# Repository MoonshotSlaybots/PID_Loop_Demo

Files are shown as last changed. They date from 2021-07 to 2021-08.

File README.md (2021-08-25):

# PID_Loop_Demo
Arduino project to demonstrate how to tune a PID controller

## [Wiki](https://github.com/MoonshotSlaybots/PID_Loop_Demo/wiki)

## Wiring Diagram
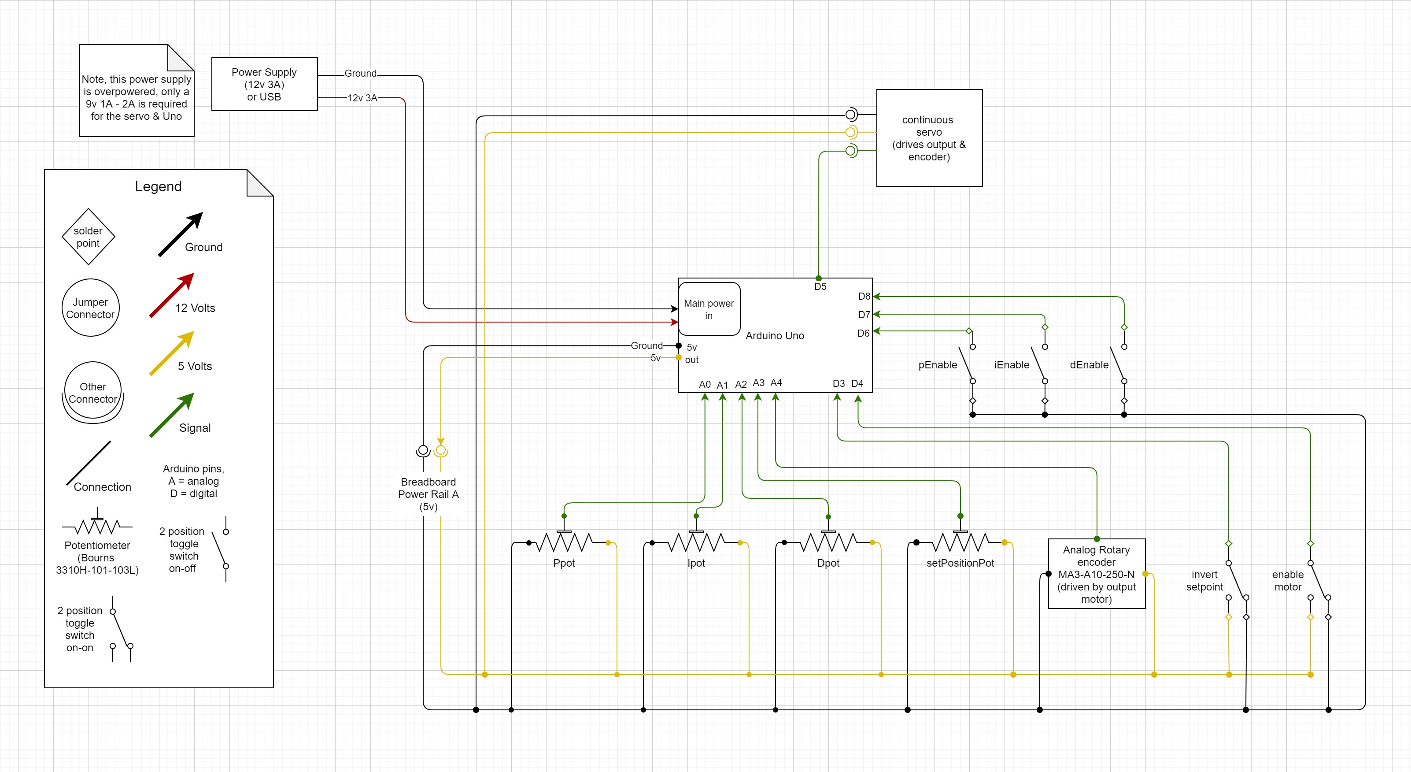
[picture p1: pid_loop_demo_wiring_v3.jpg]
Wiring Diagram


## Major Tools Needed
- 3D printer (small parts)
- Laser cutter (at least 12 in. by 6 in.)

## Hardware list
- 1 x [Arduino Uno](https://store.arduino.cc/usa/arduino-uno-rev3)
- 4 x [10Kohm Potentiometer](https://www.mouser.com/ProductDetail/Bourns/3310H-101-103L?qs=gTYE2QTfZfRCK85Ji3ROkA%3D%3D)
- 1 x [Continuous Servo (HSR-1425CR)](https://www.andymark.com/products/hi-tec-servo-model-hsr-1425cr?sku=am-2587)
- 3 x [ON - OFF Toggle Switches](https://www.amazon.com/mxuteuk-Terminal-Position-Miniature-Dashboard/dp/B07QGDDTWJ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)
- 2 x ON - ON Toggle Switches
- 24 x [Hex Drive Flat Head Screw, 10-32 Thread Size, 3/8" Long](https://www.mcmaster.com/91253A001/)
- 24 x [Brass Heat-Set Inserts for Plastic](https://www.mcmaster.com/97171A200/)
- 3mm plywood for laser cut
- PLA Filament for 3D print

## Known Issues
- Running the servo power on the same circuit as the inputs causes significant voltage drops when the servo starts moving. The input potentiometers see this voltage change as a change in the input and creates noise in the system. This is because the inputs are analog and sensitive to voltage changes. This could be corrected by isolating the control circuit from the servo power draw or by using a digital method for the input, such as pwm. 
- Crossing from -180 deg to 180 deg creates a hiccup in the system. This is likely due to the smoothing algorithm trying to smooth the large change in angle rather than an instantaneous change as it should be.
- High Kd values cuases jitter in the system, this is likely related to the power draw issue listed ealier.

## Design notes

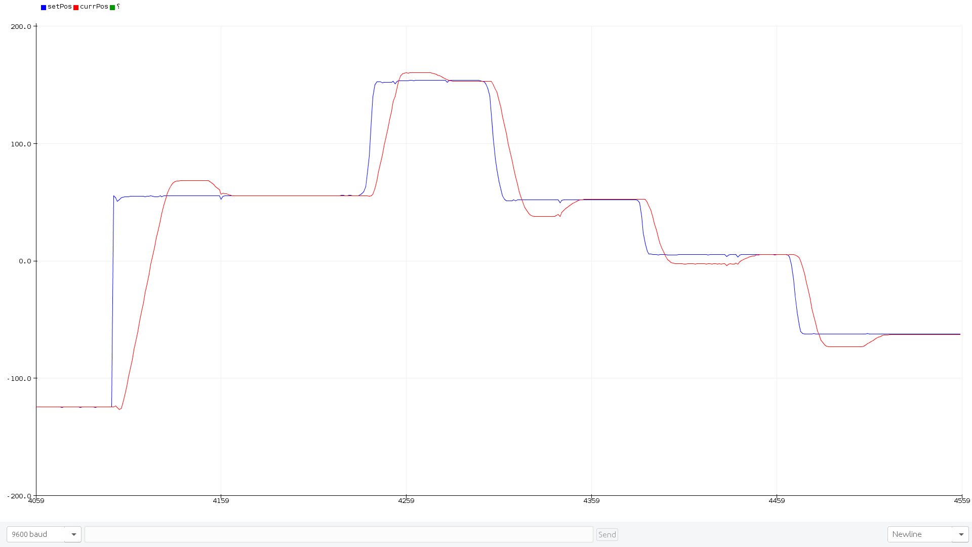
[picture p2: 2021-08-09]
images/PI_good.png

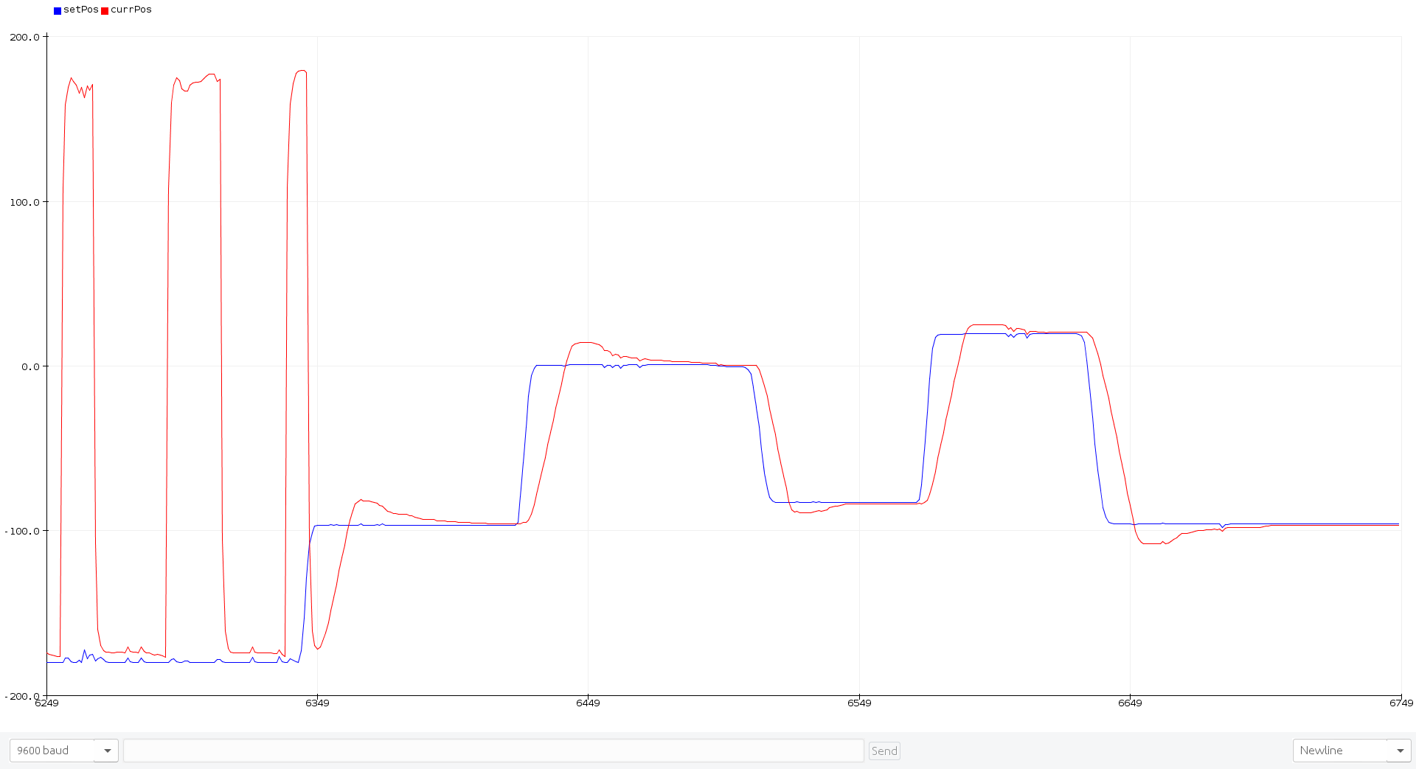
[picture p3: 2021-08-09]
images/PID_PI_only.png

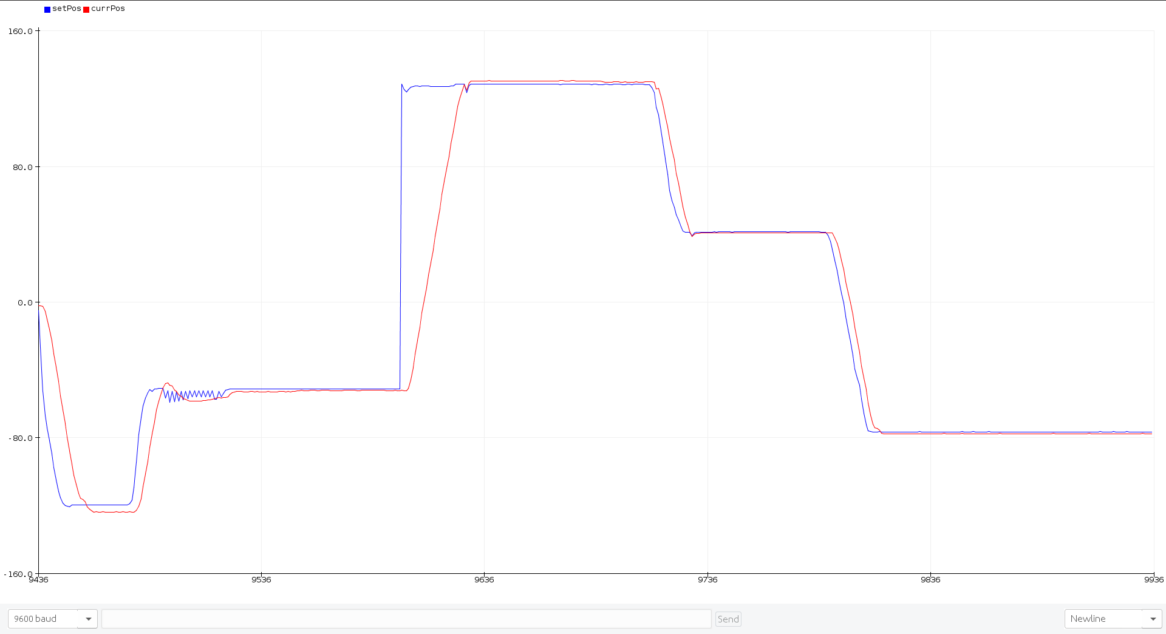
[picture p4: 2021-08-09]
images/PID_good.png

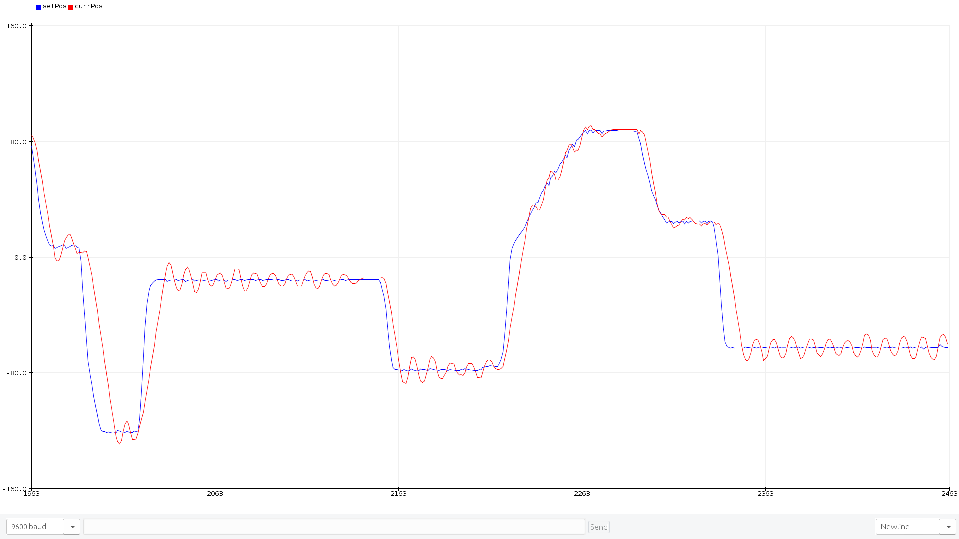
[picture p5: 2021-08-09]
images/p_too_high.png

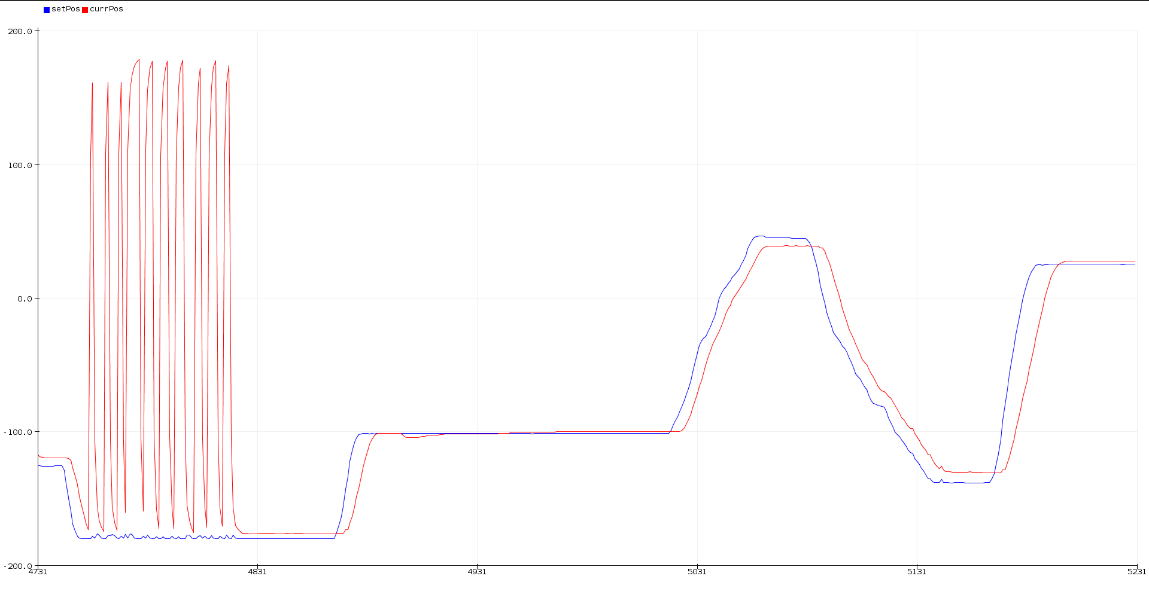
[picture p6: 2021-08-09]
images/p_good.png

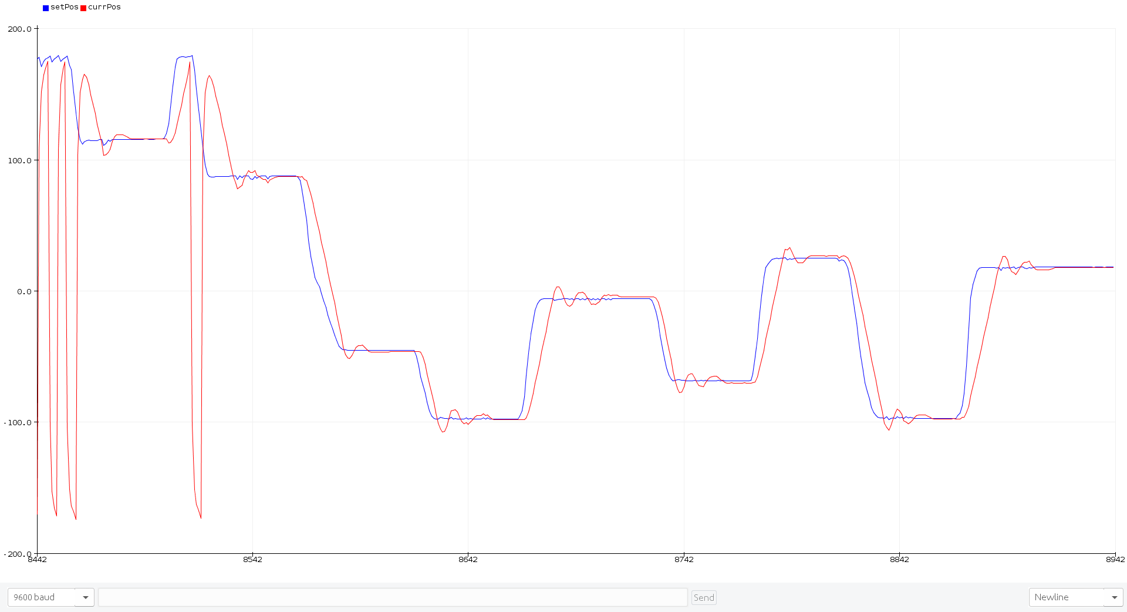
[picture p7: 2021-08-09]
images/p_little_too_high.png

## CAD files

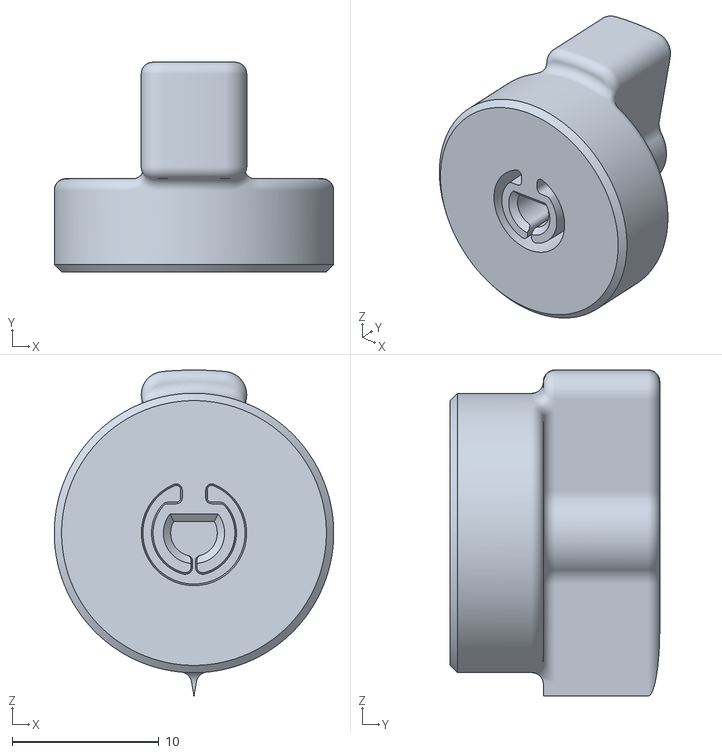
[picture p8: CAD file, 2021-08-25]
mechanical/3D_print/POT_Knob_V2.1.STL
19.0 x 14.3 x 22.2

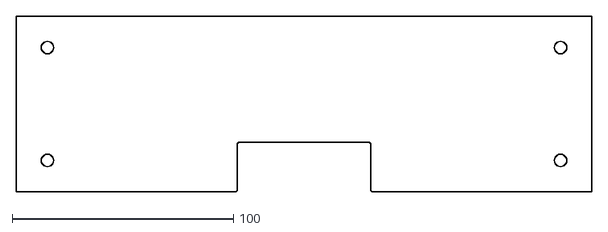
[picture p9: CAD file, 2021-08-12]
mechanical/Laser_cut/Back Panel Cut clean.dxf
260.0 x 79.2

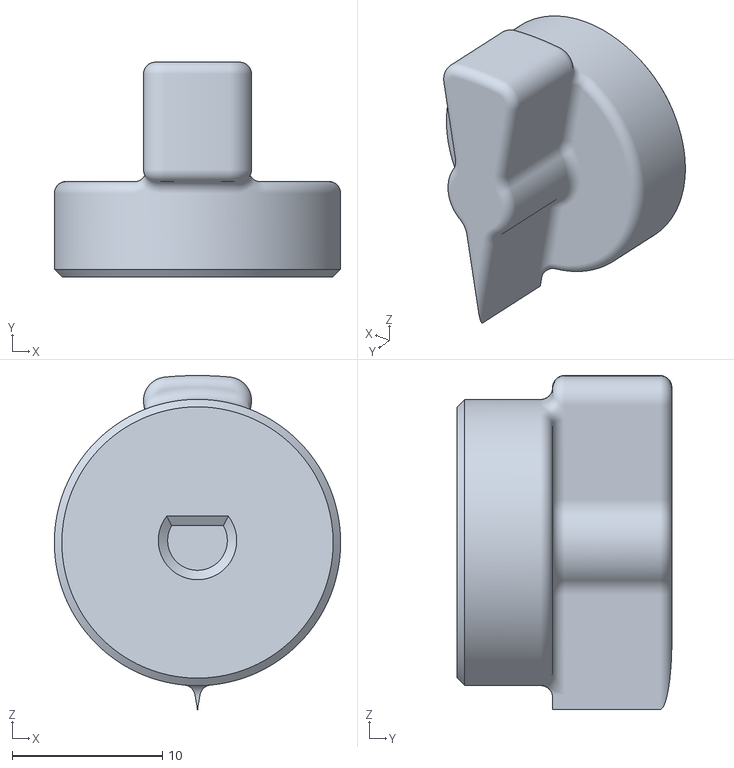
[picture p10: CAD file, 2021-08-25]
mechanical/3D_print/POT_Knob_V2_125%_hole.STL
19.0 x 14.3 x 22.2

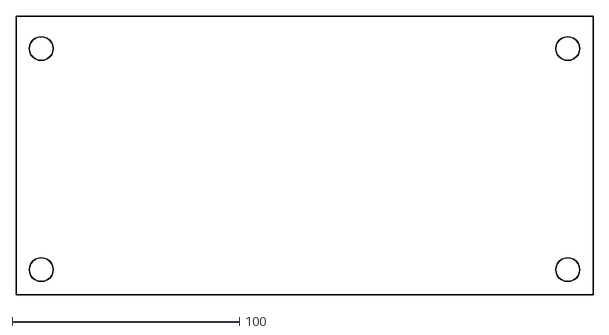
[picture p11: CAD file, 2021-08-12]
mechanical/Laser_cut/Bottom Panel Engrave clean.dxf
254.0 x 122.7

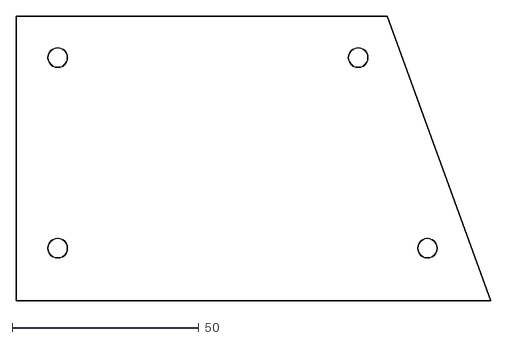
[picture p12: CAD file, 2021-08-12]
mechanical/Laser_cut/Left Panel Cut clean.dxf
127.0 x 76.2

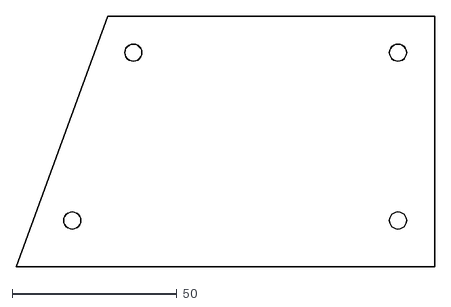
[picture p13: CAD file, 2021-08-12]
mechanical/Laser_cut/Right Panel Cut clean.dxf
127.0 x 76.2

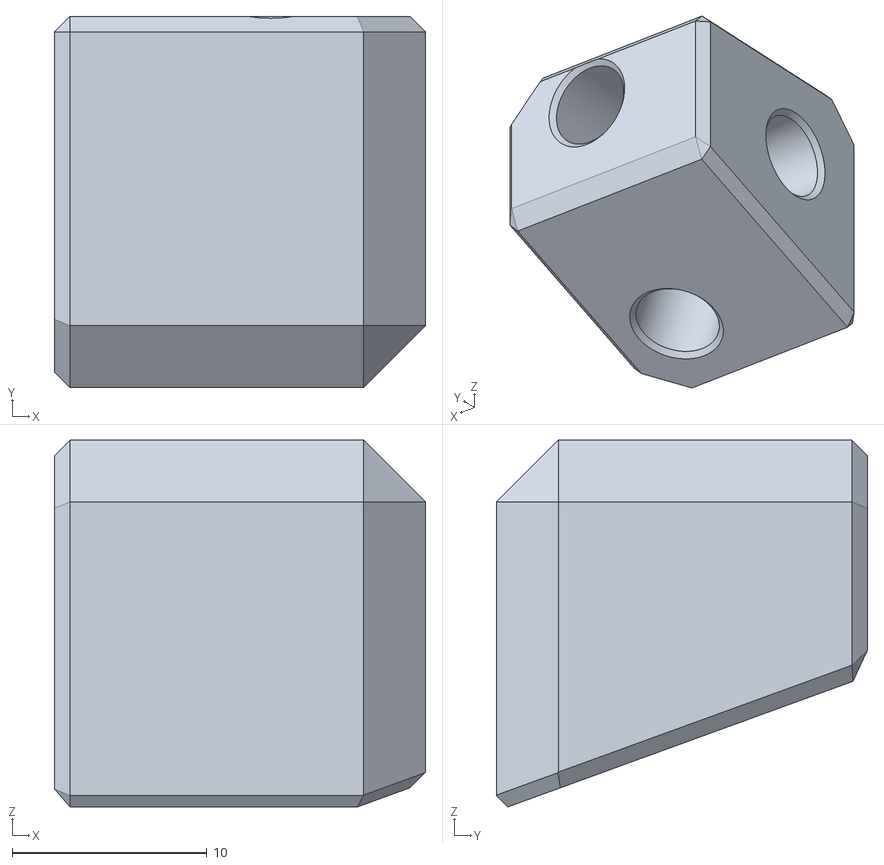
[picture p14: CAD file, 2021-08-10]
mechanical/3D_print/Front_Top_Left_Front_Corner_Block.STL
19.1 x 19.1 x 18.8

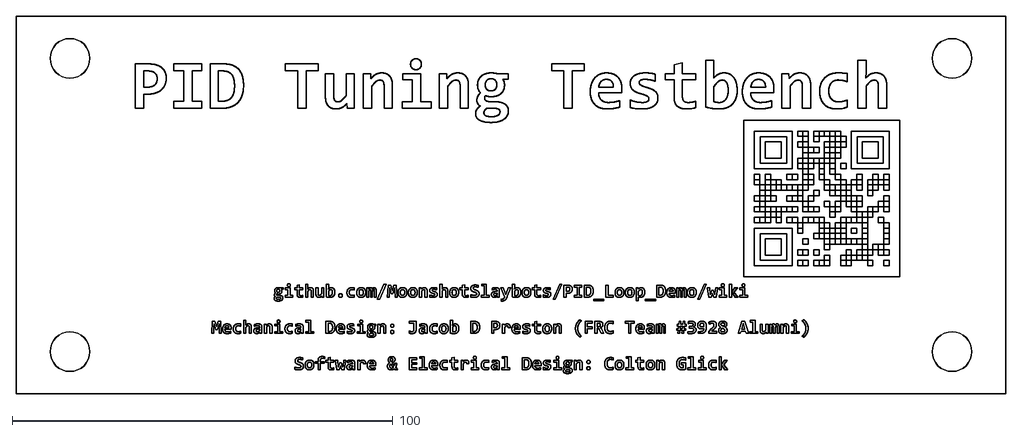
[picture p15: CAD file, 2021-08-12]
mechanical/Laser_cut/Top Panel Engrave filled.dxf
260.0 x 99.3

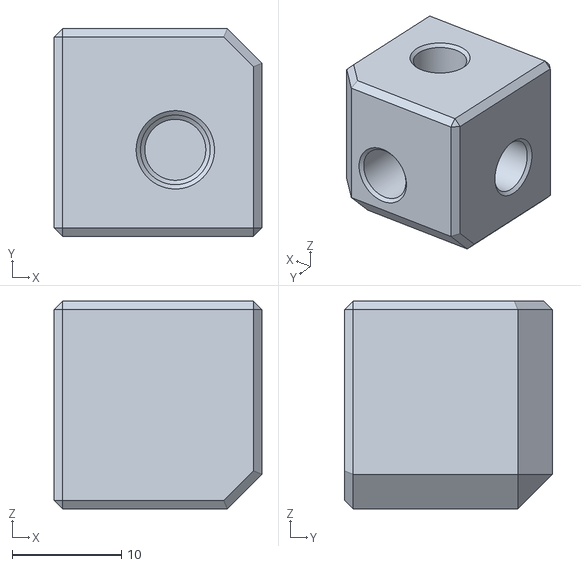
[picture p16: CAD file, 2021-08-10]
mechanical/3D_print/Back_3_Way_90_deg_Corner_Block_V1.STL
19.1 x 19.1 x 19.1

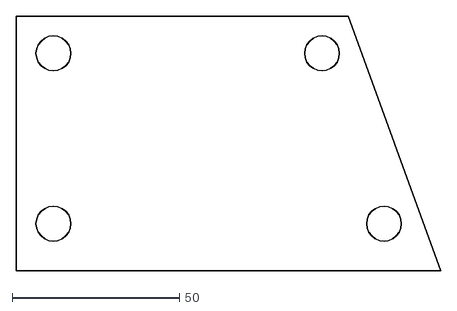
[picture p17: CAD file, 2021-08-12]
mechanical/Laser_cut/Left Panel Engrave clean.dxf
127.0 x 76.2

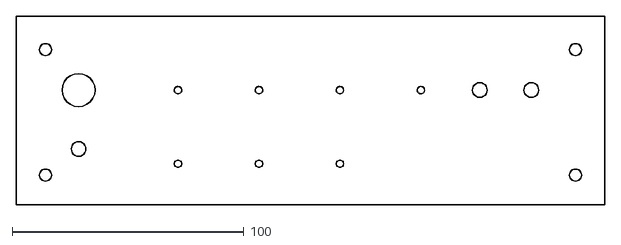
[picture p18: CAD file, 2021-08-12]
mechanical/Laser_cut/Front Panel Cut clean.dxf
254.0 x 81.1

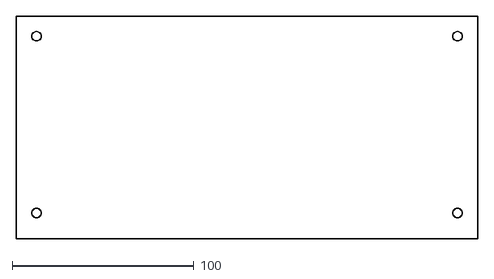
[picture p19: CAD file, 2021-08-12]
mechanical/Laser_cut/Bottom Panel Cut clean.dxf
254.0 x 122.7

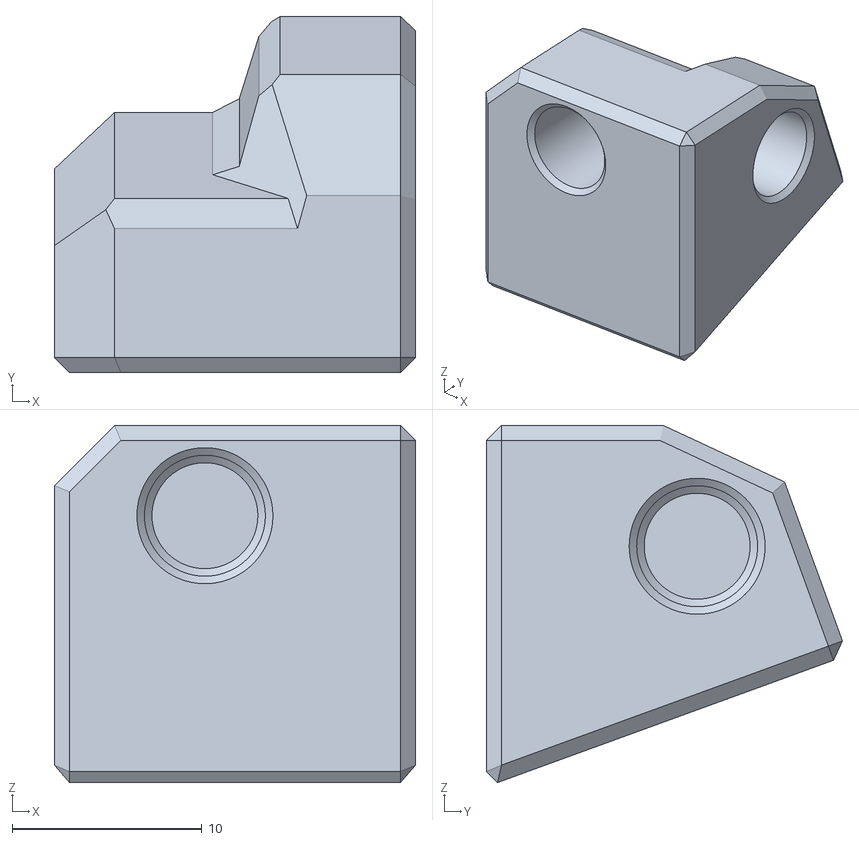
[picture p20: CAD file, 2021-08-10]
mechanical/3D_print/Front_Bottom_Right_Front_Corner_Block.STL
19.1 x 18.8 x 18.8

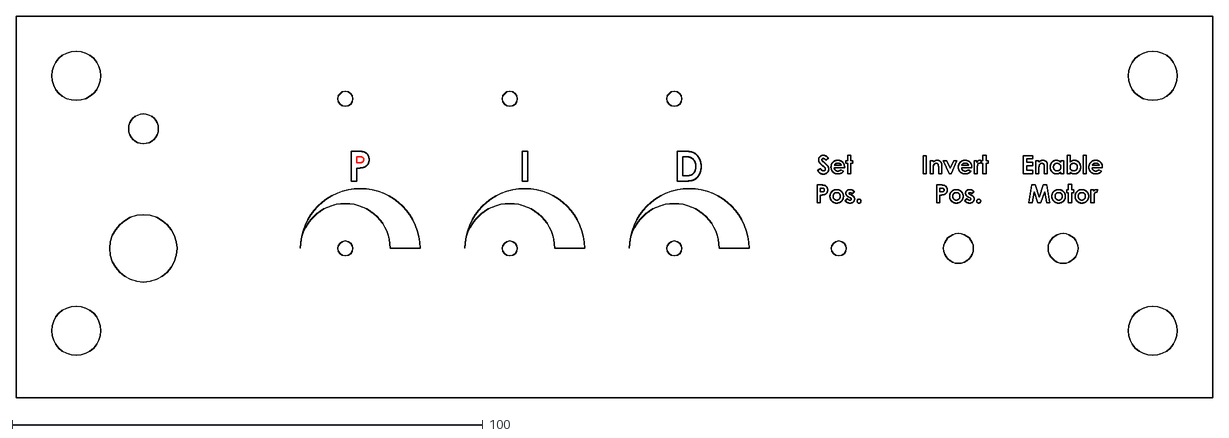
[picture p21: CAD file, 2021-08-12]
mechanical/Laser_cut/Front Panel Engrave filled.dxf
254.0 x 81.1

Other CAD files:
mechanical/3D_print/Front_Bottom_Left_Front_Corner_Block.STL
mechanical/3D_print/Front_Top_Right_Front_Corner_Block.STL
mechanical/Laser_cut/Right Panel Engrave clean.dxf
mechanical/Laser_cut/Back Panel Engrave clean.dxf
mechanical/3D_print/POT_Knob_V2.STL
mechanical/3D_print/POT_Knob_V2_123%_hole.STL
mechanical/Laser_cut/Back Panel Cut.DXF
mechanical/Laser_cut/Back Panel Engrave.DXF
mechanical/Laser_cut/Bottom Panel Cut.DXF
mechanical/Laser_cut/Bottom Panel Engrave.DXF
mechanical/Laser_cut/Front Panel Cut.DXF
mechanical/Laser_cut/Front Panel Engrave.DXF
mechanical/Laser_cut/Left Panel Cut.DXF
mechanical/Laser_cut/Left Panel Engrave.DXF
mechanical/Laser_cut/Right Panel Cut.DXF
mechanical/Laser_cut/Right Panel Engrave.DXF
mechanical/Laser_cut/Top Panel Cut clean.dxf
mechanical/Laser_cut/Top Panel Cut.DXF
mechanical/Laser_cut/Top Panel Engrave.DXF

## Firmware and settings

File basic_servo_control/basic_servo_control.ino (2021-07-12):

/**
 * Reads the value of a potentiometer connected to analog pin 0
 * to control the speed of a continous servo plugged into digital pin 2
 */
#include <Servo.h>

int potPin = 3;   //input pin for the potentiometer
int val = 0;      //current value of the potentiometer

int servoPin = 2;   //PWM pin for the servo
Servo servo;
int maxPWM = 1750;  //in microseconds, the duty cycle PWM range to control speed
int minPWM = 1250;  //this is specific to the HSR-1425CR servo, tweak as needed for others

void setup() {
  Serial.begin(9600);
  servo.attach(servoPin);
}

void loop() {
  val = analogRead(potPin);     //read value from pot
  //Serial.println(val);
  //scale pot value to be between -1 and 1
  float s = (val - 512) / 512.0;
  Serial.println(s);
  setServoSpeed(s);
}

void setServoSpeed(float s){
  servo.writeMicroseconds(minPWM + (s+1)/2.0 * (maxPWM - minPWM));
}

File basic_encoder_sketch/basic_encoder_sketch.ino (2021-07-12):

const int encoderPin = 4;


/**
   initialize arduino for operation
*/
void setup() {
  Serial.begin(9600);   //start serial communication for console
}


/**
 * Main loop that controls the motor
 */
void loop() {
  Serial.println(readAnalogAngle(encoderPin, 1));

}

//reads the current angle (0 to 360) of the analog encoder on the given pin
//takes n samples and averages the output
float readAnalogAngle(int pin, int numSamples){
  const float minVoltage = 0.015;
  const float maxVoltage = 4.987;
  int samples[numSamples]; //0-1023

  //take samples
  for(int i=0; i<numSamples; i++){
    samples[i] = analogRead(pin); //0-1023
  }

  //find average
  float sum = 0.0;
  for(int i=0; i<numSamples; i++){
    sum += samples[i];
  }
  float voltage = (sum / numSamples)/1024 * 5.0; 

  //convert from voltage to angle
  return voltage/maxVoltage * 360;
}

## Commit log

2021-05-30 created wiring diagram
2021-06-06 added basic stepper controller sketch,
    controls the speed of a stepper with a pot
2021-06-06 Can control stepper motor speed from -1 to 1
2021-07-05 added v2 design with servo and encoder
2021-07-05 added functions to read PWM or analog encoders
2021-07-05 added v2 wiring diagram xml
2021-07-11 added sketch for basic continous servo control
2021-07-11 changed design to analog encoder
2021-07-12 testing servo and encoder together
2021-07-25 added filtering to analog inputs and other work
2021-07-26 added enable switches to P I and D inputs
2021-08-02 fixed some issues with -180 to 180, D needs to be looked at
    [PID_Demo_Sketch.ino]
2021-08-10 Added mechanical files
    [Back Panel Cut.DXF, Back Panel Engrave.DXF, Back_3_Way_90_deg_Corner_Block_V1.STL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]
2021-08-10 Added gear STLs
2021-08-12 Cleaned up laser cut panels
    [Back Panel Cut clean.dxf, Back Panel Engrave clean.dxf, Bottom Panel Cut clean.dxf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]
2021-08-16 added potentiometer knob
    [POT_Knob_V2.STL]
2021-08-17 Added new knob STLs
    [POT_Knob_V2.1.STL, POT_Knob_V2_125%_hole.STL]
2021-08-19 added angle offset for encoder
2021-08-20 updated wiring diagram
    [POT_Knob_V2_123%_hole.STL]
2021-08-20 added wiring diagram v3 xml
